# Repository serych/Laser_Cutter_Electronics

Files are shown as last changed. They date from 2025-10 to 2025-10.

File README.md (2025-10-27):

# Laser cutter electronics for Fluid NC
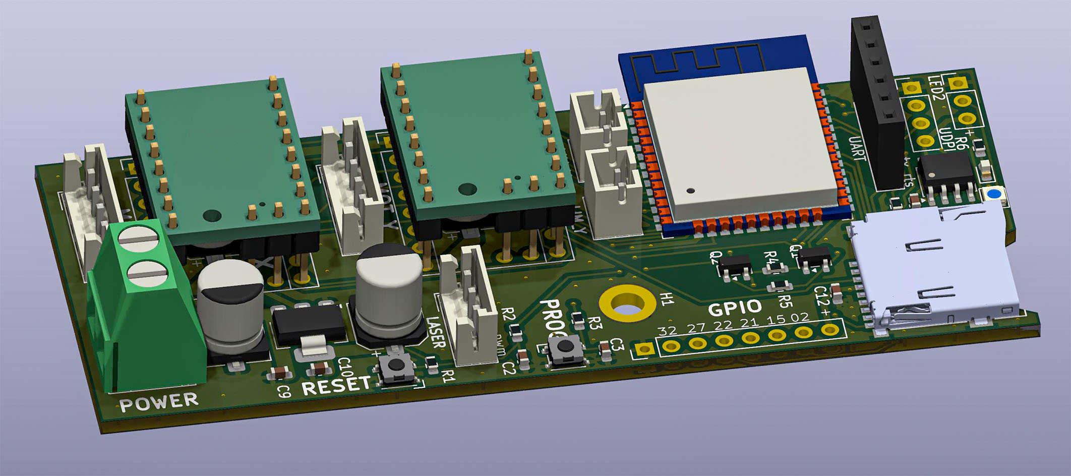
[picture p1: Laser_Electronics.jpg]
3D model of the board


This is small laser cutter electronics board. The main goal of the development was to achieve a **board width of less than 4 cm** so that it could be easily mounted on standard 4020 profiles used in the construction of laser engravers. 
The board is designed for use with [Fluid NC software](http://wiki.fluidnc.com/en/home). 
## Electronics concept
The electronics are based on the **ESP32 WROOM** module, containing two **TMC2130 SPI** stepper motor drivers, a **PWM output for the laser**, and a **Micro SD card slot**. 
The initial programming of the ESP32 processor must be done via an **external USB-UART converter**; the board has a connector for this purpose. 
**!!!Make sure that the converter supplies the board with 3.3V (and not 5V)!!!** 
Further upgrades can be done using OTA. 

The board also includes an **Attiny 412 processor**, which controls a WS2812 **color status LED** (internal with the option of connecting one additional external LED). This processor can be programmed via the UPDI interface (there is a connector on the board for this purpose), which is again connected to the USB-UART converter. 
*The Attiny 412 processor with status LED is an **optional accessory**; the board works even without it.* 
## Files
The schematic and PCB layout were created in [KiCad](https://kicad.org) 9. The Gerber and drilling files for PCB production are stored in the "Gerber" directory.

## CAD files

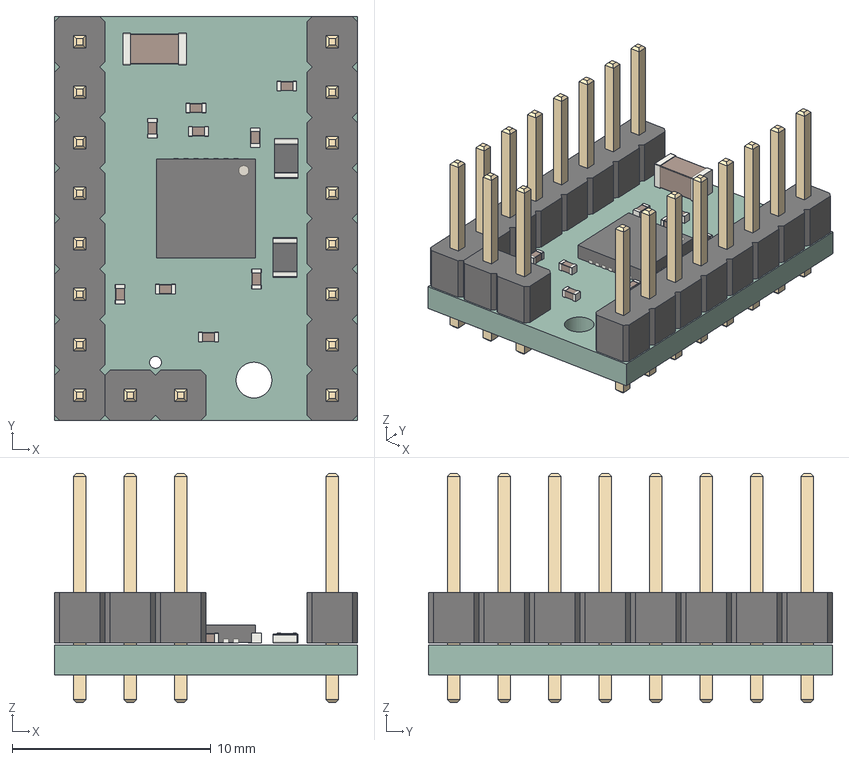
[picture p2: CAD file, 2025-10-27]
SilentStepStick-TMC2209_v20.step
15.2 x 20.3 x 11.5 mm
R_0805_2012Metric x 2
C_0402_1005Metric x 9
PinHeader_1x08_P2.54mm_Vertical x 2
PinHeader_1x02_P2.54mm_Vertical
QFN-28-1EP_5x5mm_P0.5mm_EP3.35x3.35mm
C_1206_3216Metric
SilentStepStick-TMC2209_v20_PCB

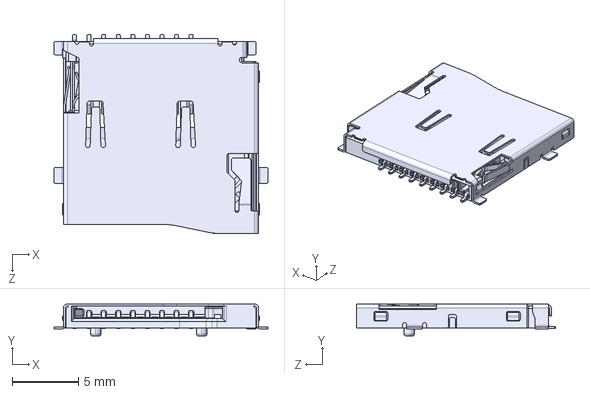
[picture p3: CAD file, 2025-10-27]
MSD-4-A.step
16.1 x 2.40 x 15.0 mm

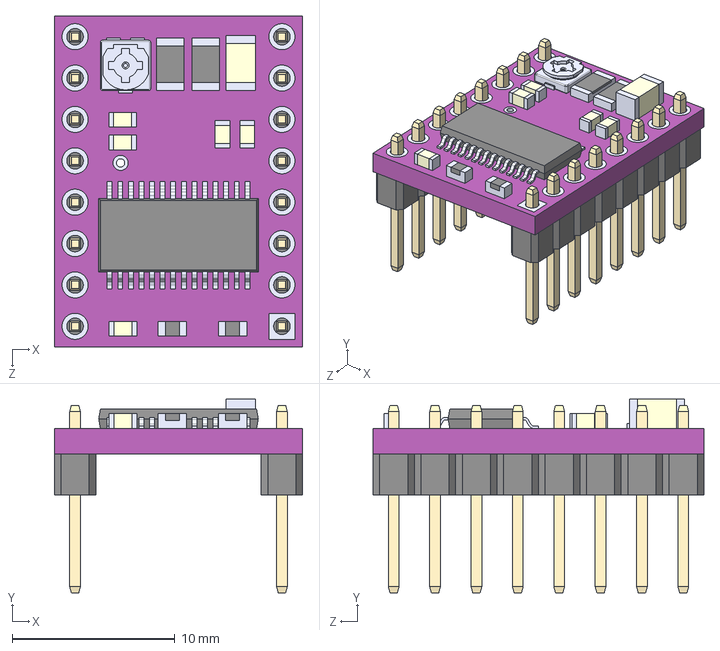
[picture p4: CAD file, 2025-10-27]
DRV8825 STEPPER MOTOR DRIVER CARRIER--3DModel-STEP-1.STEP
15.2 x 11.9 x 20.3 mm

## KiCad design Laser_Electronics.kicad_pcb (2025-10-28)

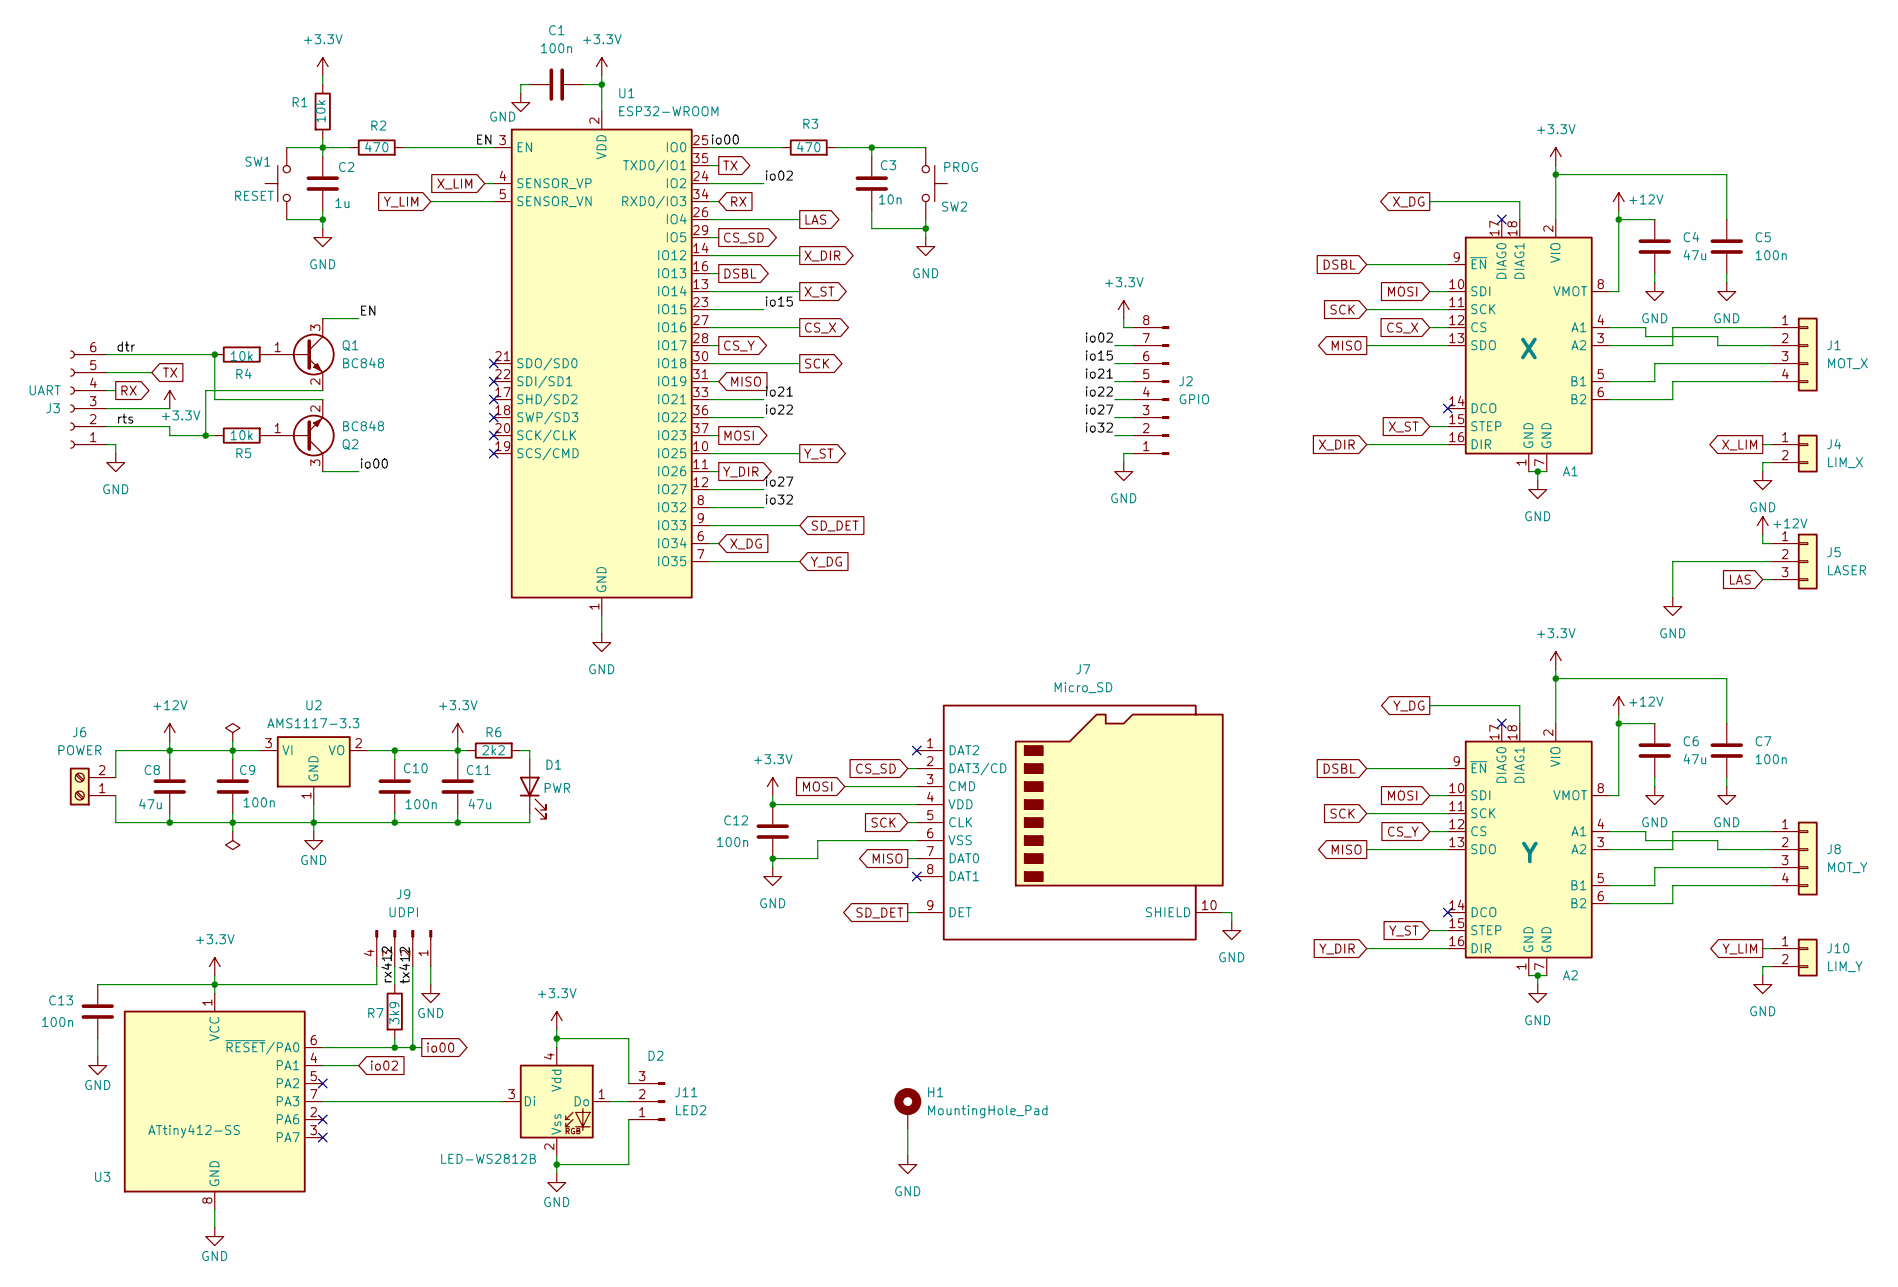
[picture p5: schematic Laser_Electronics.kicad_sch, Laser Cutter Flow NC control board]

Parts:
A1: X; Pololu_Breakout-18_15.2x20.3mm
A2: Y; Pololu_Breakout-18_15.2x20.3mm
C1, C5, C7, C9, C10, C12, C13: 100n; C_0603_1608Metric
C2: 1u; C_0603_1608Metric
C3: 10n; C_0603_1608Metric
C4, C6, C8, C11: 47u; CP_Elec_6.3x7.7
D1: PWR; LED_0603_1608Metric
D2: LED-WS2812B; LED_Cree-PLCC4_2x2mm_CW
H1: MountingHole_Pad; MountingHole_3.2mm_M3_DIN965_Pad
J1: MOT_X; JST_EH_B4B-EH-A_1x04_P2.50mm_Vertical
J2: GPIO; PinHeader_1x08_P2.54mm_Vertical
J3: UART; PinSocket_1x06_P2.54mm_Vertical
J4: LIM_X; JST_PH_B2B-PH-K_1x02_P2.00mm_Vertical
J5: LASER; JST_EH_B3B-EH-A_1x03_P2.50mm_Vertical
J6: POWER; TerminalBlock_RND_205-00045_1x02_P5.00mm_Horizontal
J7: Micro_SD; J_SD_Card-micro_socket_A
J8: MOT_Y; JST_EH_B4B-EH-A_1x04_P2.50mm_Vertical
J9: UDPI; PinHeader_1x04_P2.54mm_Vertical
J10: LIM_Y; JST_PH_B2B-PH-K_1x02_P2.00mm_Vertical
J11: LED2; PinHeader_1x03_P2.54mm_Vertical
Q1, Q2: BC848; SOT-23
R1, R4, R5: 10k; R_0603_1608Metric
R2, R3: 470; R_0603_1608Metric
R6: 2k2; R_0603_1608Metric
R7: 3k9; R_0603_1608Metric
SW1: RESET; SW_3x3mm
SW2: PROG; SW_3x3mm
U1: ESP32-WROOM; ESP32-WROOM-32
U2: AMS1117-3.3; SOT-223-3_TabPin2
U3: ATtiny412-SS; SOIC-8_3.9x4.9mm_P1.27mm

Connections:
+3.3V: A1.2 (VIO), A2.2 (VIO), C1.2, C5.2, C7.2, C10.1, C11.1, C12.2, C13.2, D2.4 (Vdd), J2.8, J3.3, J7.4 (VDD), J9.4, J11.3, R1.1, R6.1, U1.2 (VDD), U2.2 (VO), U3.1 (VCC)
+12V: A1.8 (VMOT), A2.8 (VMOT), C4.1, C6.1, C8.1, C9.1, J5.1, J6.2, U2.3 (VI)
/EN: Q1.3 (C), R2.2, U1.3 (EN)
/dtr: J3.6, Q2.2 (E), R4.1
/io15: J2.6, U1.23 (IO15)
/io21: J2.5, U1.33 (IO21)
/io22: J2.4, U1.36 (IO22)
/io27: J2.3, U1.12 (IO27)
/io32: J2.2, U1.8 (IO32)
/rts: J3.2, Q1.2 (E), R5.1
/rx412: J9.3, R7.1
CS_SD: J7.2 (DAT3/CD), U1.29 (IO5)
CS_X: A1.12 (CS), U1.27 (IO16)
CS_Y: A2.12 (CS), U1.28 (IO17)
DSBL: A1.9 (~EN), A2.9 (~EN), U1.16 (IO13)
GND: A1.1 (GND), A1.7 (GND), A2.1 (GND), A2.7 (GND), C1.1, C2.2, C3.2, C4.2, C5.1, C6.2, C7.1, C8.2, C9.2, C10.2, C11.2, C12.1, C13.1, D1.1 (K), D2.2 (Vss), H1.1, J2.1, J3.1, J4.2, J5.2, J6.1, J7.6 (VSS), J7.10 (SHIELD), J9.1, J10.2, J11.1, SW1.1, SW2.2, U1.1 (GND), U1.15 (GND), U1.38 (GND), U1.39 (GND), U2.1 (GND), U3.8 (GND)
LAS: J5.3, U1.26 (IO4)
MISO: A1.13 (SDO), A2.13 (SDO), J7.7 (DAT0), U1.31 (IO19)
MOSI: A1.10 (SDI), A2.10 (SDI), J7.3 (CMD), U1.37 (IO23)
unnamed: A1.4 (A1), J1.2
unnamed: A1.3 (A2), J1.1
unnamed: A1.5 (B1), J1.3
unnamed: A1.6 (B2), J1.4
unnamed: A2.4 (A1), J8.2
unnamed: A2.3 (A2), J8.1
unnamed: A2.5 (B1), J8.3
unnamed: A2.6 (B2), J8.4
unnamed: C2.1, R1.2, R2.1, SW1.2
unnamed: C3.1, R3.2, SW2.1
unnamed: D1.2 (A), R6.2
unnamed: D2.3 (Di), U3.7 (PA3)
unnamed: D2.1 (Do), J11.2
unnamed: Q1.1 (B), R4.2
unnamed: Q2.1 (B), R5.2
RX: J3.4, U1.34 (RXD0/IO3)
SCK: A1.11 (SCK), A2.11 (SCK), J7.5 (CLK), U1.30 (IO18)
SD_DET: J7.9 (DET), U1.9 (IO33)
TX: J3.5, U1.35 (TXD0/IO1)
X_DG: A1.18 (DIAG1), U1.6 (IO34)
X_DIR: A1.16 (DIR), U1.14 (IO12)
X_LIM: J4.1, U1.4 (SENSOR_VP)
X_ST: A1.15 (STEP), U1.13 (IO14)
Y_DG: A2.18 (DIAG1), U1.7 (IO35)
Y_DIR: A2.16 (DIR), U1.11 (IO26)
Y_LIM: J10.1, U1.5 (SENSOR_VN)
Y_ST: A2.15 (STEP), U1.10 (IO25)
io00: J9.2, Q2.3 (C), R3.1, R7.2, U1.25 (IO0), U3.6 (~RESET/PA0)
io02: J2.7, U1.24 (IO2), U3.4 (PA1)

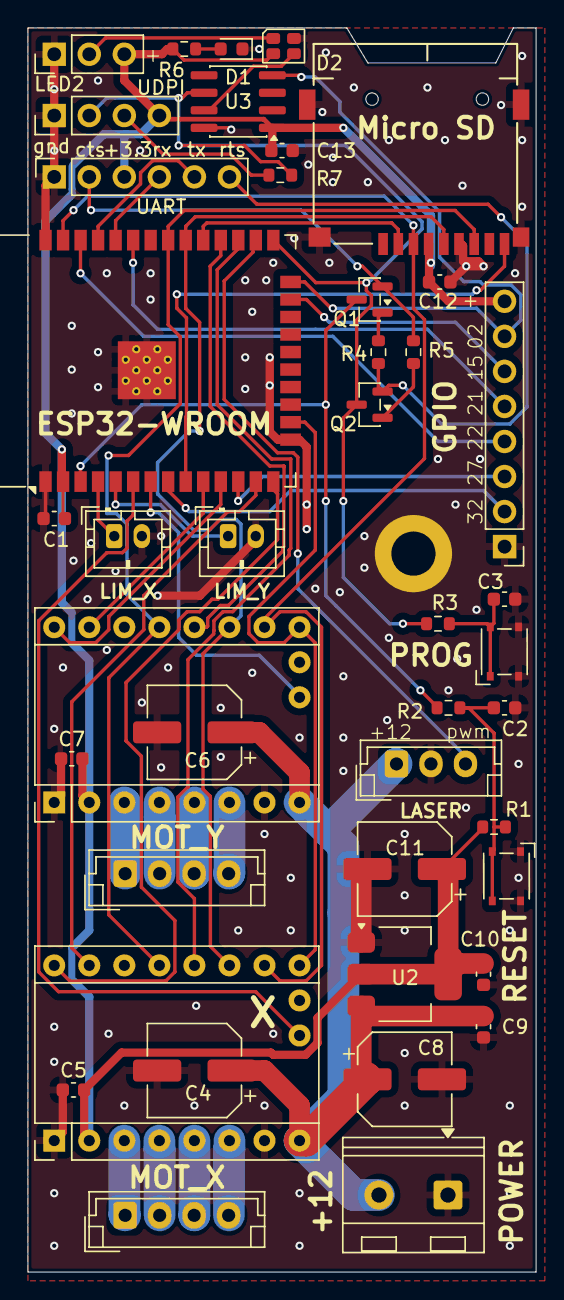
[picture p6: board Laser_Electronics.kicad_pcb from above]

Board: 2 copper layers, 36.8 x 90.2 mm, 43 parts (0 on the bottom side), 48 nets.

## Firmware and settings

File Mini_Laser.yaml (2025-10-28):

name: Mini TMC2130 XY Laser
board: Mini Laser Electronics
status_outputs:
  report_interval_ms: 500
  run_pin: NO_PIN
uart1:
  txd_pin: gpio.2
  rxd_pin: gpio.0
  rts_pin: NO_PIN
  baud: 115200
  mode: 8N1
uart_channel1:
  uart_num: 1
  report_interval_ms: 500
stepping:
  engine: RMT
  idle_ms: 255
  dir_delay_us: 1
  pulse_us: 2
  disable_delay_us: 0
axes:
  shared_stepper_disable_pin: gpio.13
  x:
    steps_per_mm: 800
    max_rate_mm_per_min: 2000
    acceleration_mm_per_sec2: 25
    max_travel_mm: 1000
    soft_limits: false
    homing:
      cycle: 2
      positive_direction: false
      mpos_mm: 5
      feed_mm_per_min: 100
      seek_mm_per_min: 200
      settle_ms: 500
      seek_scaler: 1.1
      feed_scaler: 1.1
    motor0:
      limit_neg_pin: gpio.36:low
      tmc_2130:
        direction_pin: gpio.12
        step_pin: gpio.14
        cs_pin: gpio.16
        r_sense_ohms: 0.11
        run_amps: 0.25
        hold_amps: 0.25
        microsteps: 32
        stallguard: 0
        stallguard_debug: false
        toff_disable: 0
        toff_stealthchop: 5
        toff_coolstep: 3
        run_mode: StealthChop
        homing_mode: StealthChop
        use_enable: false
      limit_pos_pin: NO_PIN
      limit_all_pin: NO_PIN
    motor1:
      limit_neg_pin: NO_PIN
      limit_pos_pin: NO_PIN
      limit_all_pin: NO_PIN
  y:
    steps_per_mm: 800
    max_rate_mm_per_min: 2000
    acceleration_mm_per_sec2: 25
    max_travel_mm: 1000
    soft_limits: false
    homing:
      cycle: 2
      positive_direction: false
      mpos_mm: 150
      feed_mm_per_min: 100
      seek_mm_per_min: 200
      settle_ms: 500
      seek_scaler: 1.1
      feed_scaler: 1.1
    motor0:
      limit_neg_pin: gpio.39:low
      tmc_2130:
        direction_pin: gpio.26
        step_pin: gpio.25
        cs_pin: gpio.17
        r_sense_ohms: 0.11
        run_amps: 0.25
        hold_amps: 0.25
        microsteps: 32
        stallguard: 0
        stallguard_debug: false
        toff_disable: 0
        toff_stealthchop: 5
        toff_coolstep: 3
        run_mode: StealthChop
        homing_mode: StealthChop
        use_enable: false
      limit_pos_pin: NO_PIN
      limit_all_pin: NO_PIN
    motor1:
      limit_neg_pin: NO_PIN
      limit_pos_pin: NO_PIN
      limit_all_pin: NO_PIN
  z:
    steps_per_mm: 100
    max_rate_mm_per_min: 1000
    acceleration_mm_per_sec2: 50
    max_travel_mm: 5
    soft_limits: false
    homing:
      cycle: 1
      positive_direction: true
      mpos_mm: 5
      feed_mm_per_min: 100
      seek_mm_per_min: 200
      settle_ms: 500
      seek_scaler: 1.1
      feed_scaler: 1.1
    motor0:
      rc_servo:
        pwm_hz: 50
        output_pin: NO_PIN
        min_pulse_us: 1000
        max_pulse_us: 2100
      limit_neg_pin: NO_PIN
      limit_pos_pin: NO_PIN
      limit_all_pin: NO_PIN
spi:
  miso_pin: gpio.19
  mosi_pin: gpio.23
  sck_pin: gpio.18
sdcard:
  cs_pin: gpio.5
  card_detect_pin: gpio.33
coolant:
  flood_pin: NO_PIN
  mist_pin: NO_PIN
probe:
  pin: NO_PIN
  toolsetter_pin: NO_PIN
Laser:
  pwm_hz: 5000
  output_pin: gpio.4
  enable_pin: NO_PIN
  disable_with_s0: false
  s0_with_disable: true
  tool_num: 0
  speed_map: 0=0.000% 255=100.000%
  off_on_alarm: true

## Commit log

2025-10-14 Hotové schéma
    [Laser_Electronics.kicad_pcb, Laser_Electronics.kicad_sch]
2025-10-27 ver 1 layout
    [DRV8825 STEPPER MOTOR DRIVER CARRIER--3DModel-STEP-1.STEP, Laser_Electronics.kicad_pcb, Laser_Electronics.kicad_sch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]
2025-10-27 Version 1 - fabrication files
    [Laser_Electronics-B_Cu.gbl, Laser_Electronics-B_Mask.gbs, Laser_Electronics-B_Paste.gbp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]
2025-10-27 Update KiCad link in README.md
2025-10-27 UART reset circuit error repaired
    [Laser_Electronics-B_Cu.gbl, Laser_Electronics-B_Mask.gbs, Laser_Electronics-B_Paste.gbp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]
2025-10-28 rev2 silkscreen + MiniLaser.yaml
    [Laser_Electronics-B_Cu.gbl, Laser_Electronics-B_Mask.gbs, Laser_Electronics-B_Paste.gbp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]

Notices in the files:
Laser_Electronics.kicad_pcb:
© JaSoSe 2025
